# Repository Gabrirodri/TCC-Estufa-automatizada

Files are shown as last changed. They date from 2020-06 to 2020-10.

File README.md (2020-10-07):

# TCC-Estufa-automatizada 2016
## Projeto de TCC de eletroeletronica, automação de estufa 

Um sistema de irrigação controlado por um PIC 18F4550.
Sistema que faz a leitura de valores gravados na EPROM(memória), 
que podem ser alterados pelo usuário através de um painel, e faz um controle de temperatura e da irrigação, 
levando em conta se o solo está com a quantidade de água adequada.

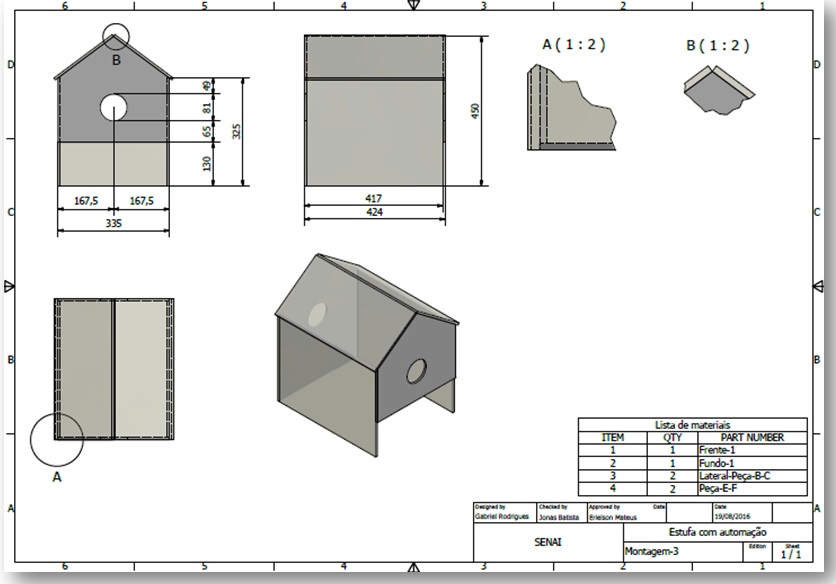
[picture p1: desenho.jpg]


## Checklist
- [X] Planejamento (Ideias de projeto, plano de ação, 5W2H)
- [X] Orçamento
- [X] Montagem do Cronograma (Divisão das tarefas)
- [X] Fluxograma
- [X] Pesquisa
- [X] Desenho da estrutura
- [X] Desenho do Circuito
- [X] Com base no fluxograma, pensar na logica de programação
- [X] Ler o Datasheet do PIC e consultar sempre quando necessario
- [X] Montagem da logica do menu
- [X] Montagem do keypad com LCD
- [X] Programação dos sensores
- [X] Aquisições de materiais, componentes, acrilicos
- [X] Fazer cortes necessarios dos acrilicos
- [X] Fazer cortes das calhas
- [X] Montagem fisica do projeto
- [X] Testes em protoboard
- [X] Confecção das placas de circuito
- [X] Soldagem de componentes
- [X] Interligação eletrica
- [X] Testes no caimento da agua das calhas
- [X] Testes no circuito: sensores, Keypad, LCD, Reles, Bomba d'agua
- [X] Correções no projeto
- [X] Testes em geral
- [X] Confecção dos manuais

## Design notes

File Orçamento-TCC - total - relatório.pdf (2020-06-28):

Materiais | Quantidade | Preço Unidade | Preço Final
Cooler | 2 | R$ 10,00 | R$ 20,00
PIC 18F4550 | 1 | R$ 40,15 | R$ 40,15
Display LCD 16x4 | 1 | R$ 16,00 | R$ 16,00
Teclado Matricial (Keypad) | 1 | R$ 13,00 | R$ 13,00
Botão de Emergência | 1 | R$ 15,00 | R$ 15,00
Bomba para Gotejamento | 1 | R$ 21,00 | R$ 21,00
Bomba para Nebulização | 1 | R$ 45,00 | R$ 45,00
Reservatório | 1 | R$ 25,00 | R$ 25,00
Acrílico | 4 | R$ 40,00 | R$ 160,00
Mangueiras | 1,5 metros | R$ 0,60 | R$ 0,90
Resistência Elétrica | 1 | R$ 30,00 | R$ 30,00
Caixa Plástica | 1 | R$ 20,00 | R$ 20,00
Caixa | 1 | R$ 30,00 | R$ 30,00
Base de Madeira | 1 | R$ 65,00 | R$ 65,00
Cano de PVC | 1,5 metros | R$ 10,00 | R$ 15,00
LED | 6 | R$ 1,50 | R$ 9,00
Sensor de Temperatura e Umidade | 1 | R$ 6,00 | R$ 6,00
Push button | 6 | R$ 3,00 | R$ 18,00
Sensor de Umidade | 1 | R$ 10,00 | R$ 10,00
Total | | | R$ 559,05

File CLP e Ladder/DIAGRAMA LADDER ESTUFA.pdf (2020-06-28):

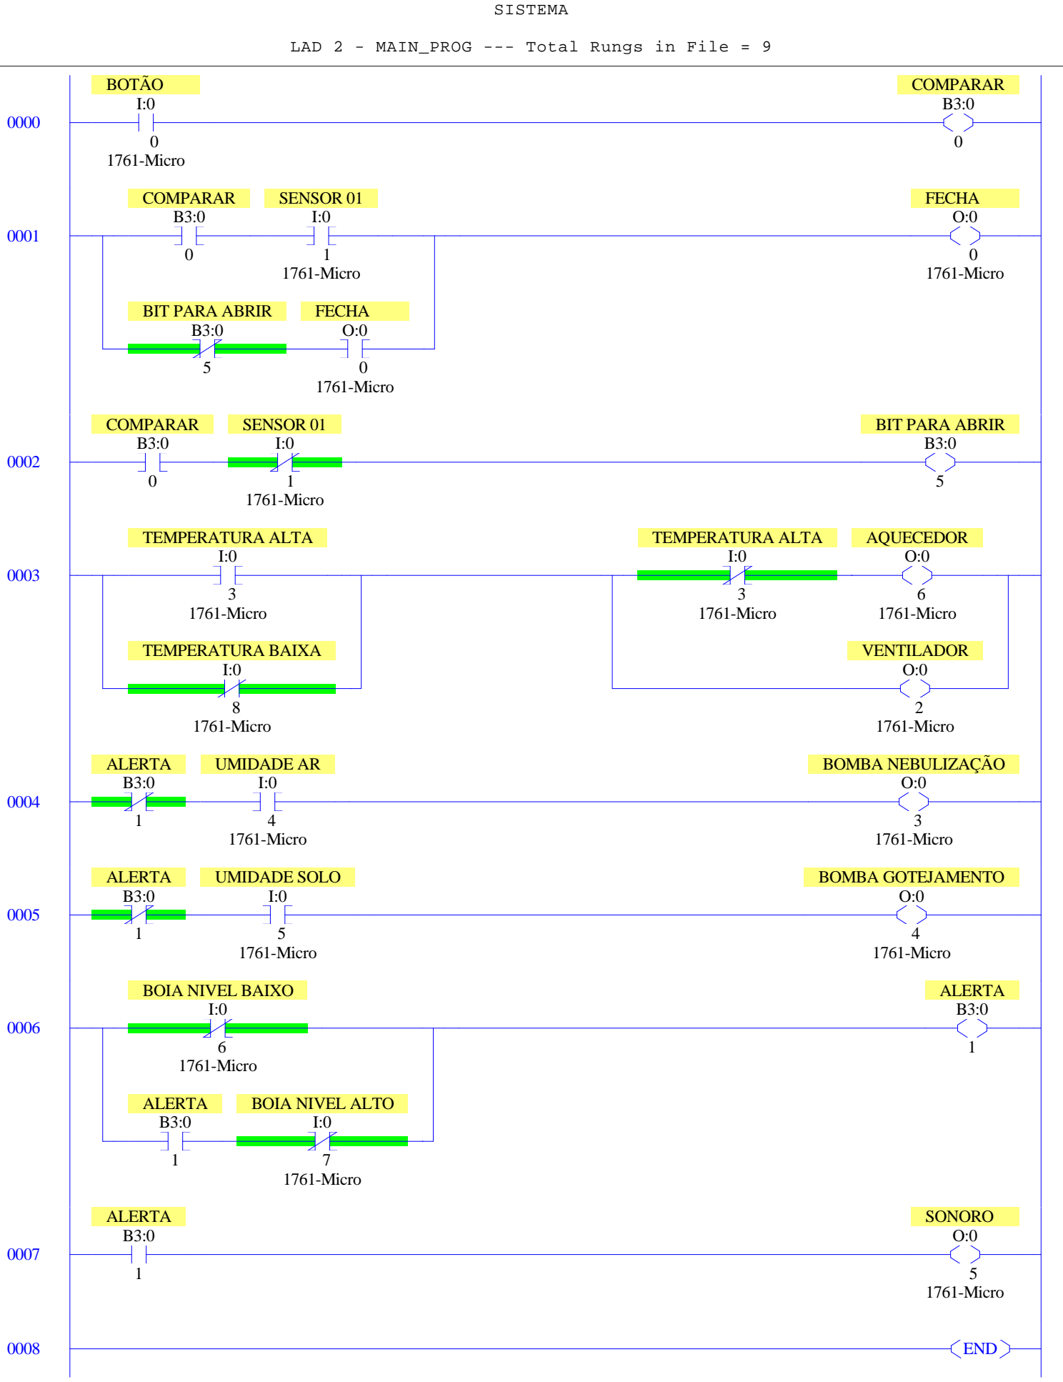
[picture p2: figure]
SISTEMA; 0 1761-Micro; BOTÃO; COMPARAR; 1 1761-Micro; SENSOR 01; BIT PARA ABRIR; FECHA; 3 1761-Micro; TEMPERATURA ALTA; 8 1761-Micro; TEMPERATURA BAIXA; 6 1761-Micro; AQUECEDOR; 2 1761-Micro; VENTILADOR; ALERTA; 4 1761-Micro; UMIDADE AR; BOMBA NEBULIZAÇÃO; 5 1761-Micro; UMIDADE SOLO; BOMBA GOTEJAMENTO; BOIA NIVEL BAIXO; 7 1761-Micro; BOIA NIVEL ALTO; SONORO; END

LAD 2 - MAIN_PROG --- Total Rungs in File = 9

Page 0 | Monday, October 31, 2016 - 15:10:52

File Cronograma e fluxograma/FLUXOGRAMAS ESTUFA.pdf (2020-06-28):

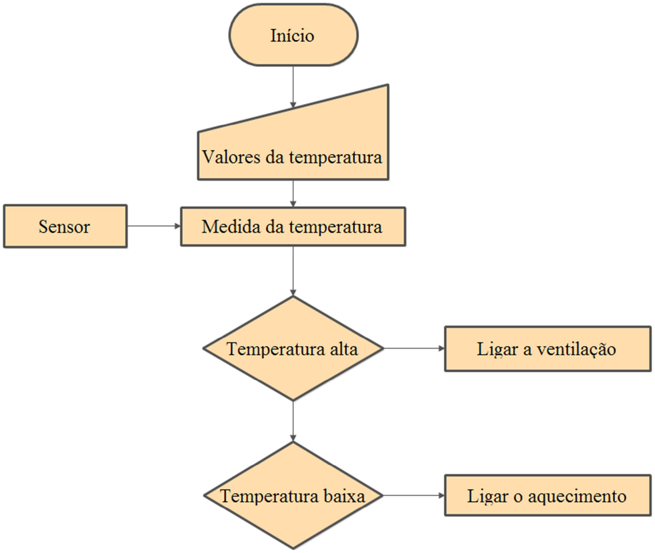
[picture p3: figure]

Lógica do controle de temperatura

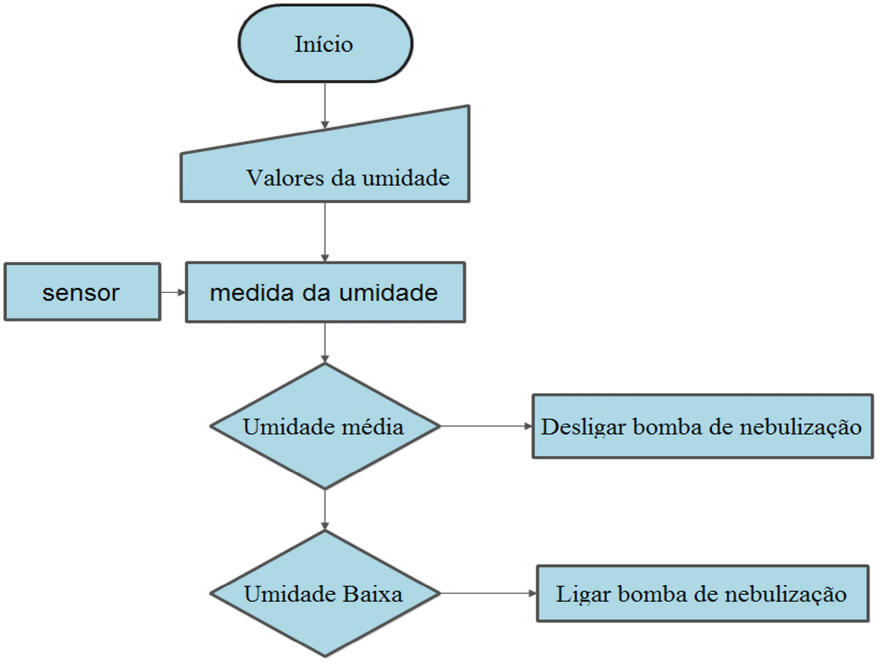
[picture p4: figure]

Lógica do controle de umidade

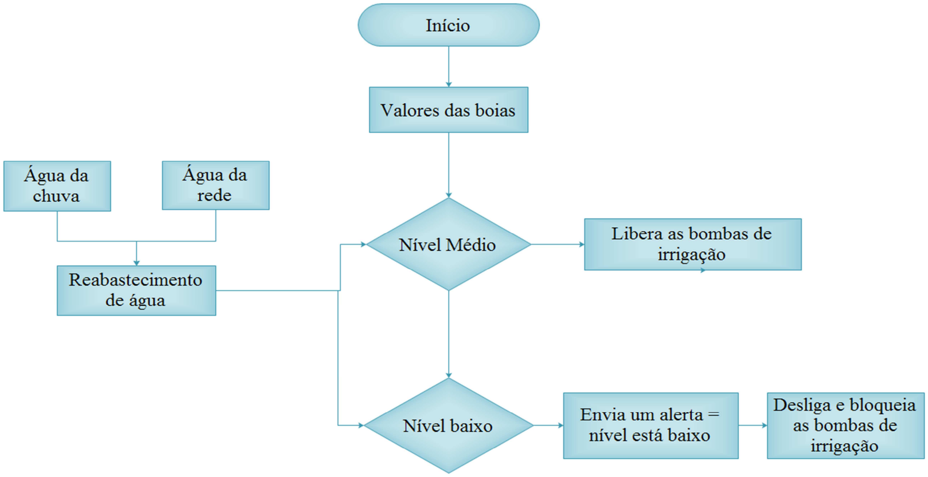
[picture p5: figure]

Lógica do controle de nível

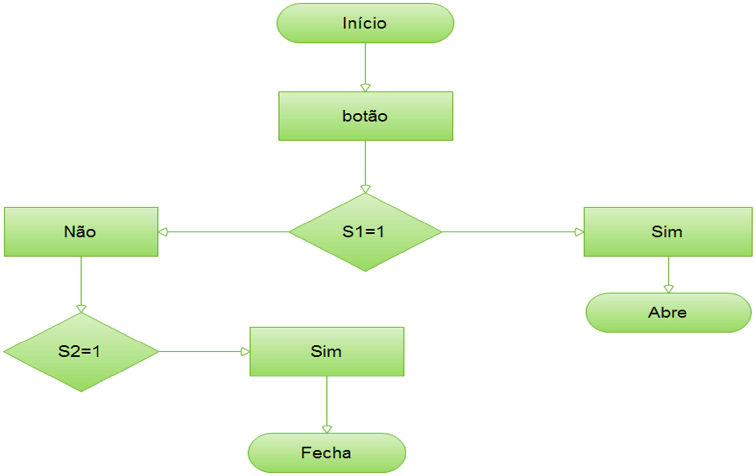
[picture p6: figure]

Lógica do controle da porta

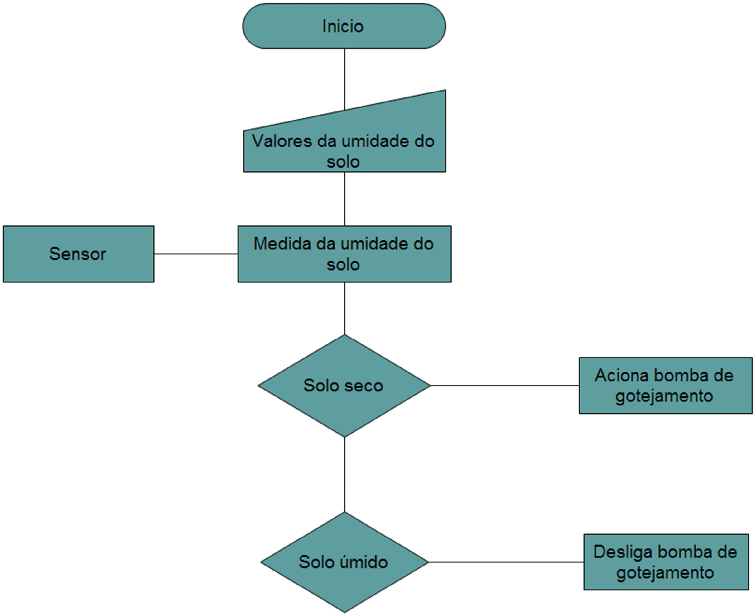
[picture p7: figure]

Controle de umidade do solo

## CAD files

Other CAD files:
TCC/Assembly1.iam
TCC/Assembly2.iam
TCC/Frente inferior - porta.ipt
TCC/Frente inferior - porta1.ipt
TCC/Frente-inferior-E-D.ipt
TCC/Montagem-2.idw
TCC/Montagem-3.idw
TCC/Montagem.iam
TCC/Montagem.idw
TCC/OldVersions/Montagem-3.0001.idw
TCC/OldVersions/Montagem.0001.idw
TCC/OldVersions/Montagem.0004.iam
TCC/OldVersions/Peças frente inferior.0001.idw
TCC/OldVersions/frente.0003.ipt
TCC/OldVersions/fundo-1.0001.idw
TCC/OldVersions/fundo.0003.ipt
TCC/OldVersions/teto01.0006.ipt
TCC/Peças frente inferior.idw
TCC/frente-1.idw
TCC/frente.idw
TCC/frente.ipt
TCC/fundo-1.idw
TCC/fundo.idw
TCC/fundo.ipt
TCC/lateral-peça-b-c.idw
TCC/lateral.ipt
TCC/teto01.idw
TCC/teto01.ipt
TCC/teto02.ipt

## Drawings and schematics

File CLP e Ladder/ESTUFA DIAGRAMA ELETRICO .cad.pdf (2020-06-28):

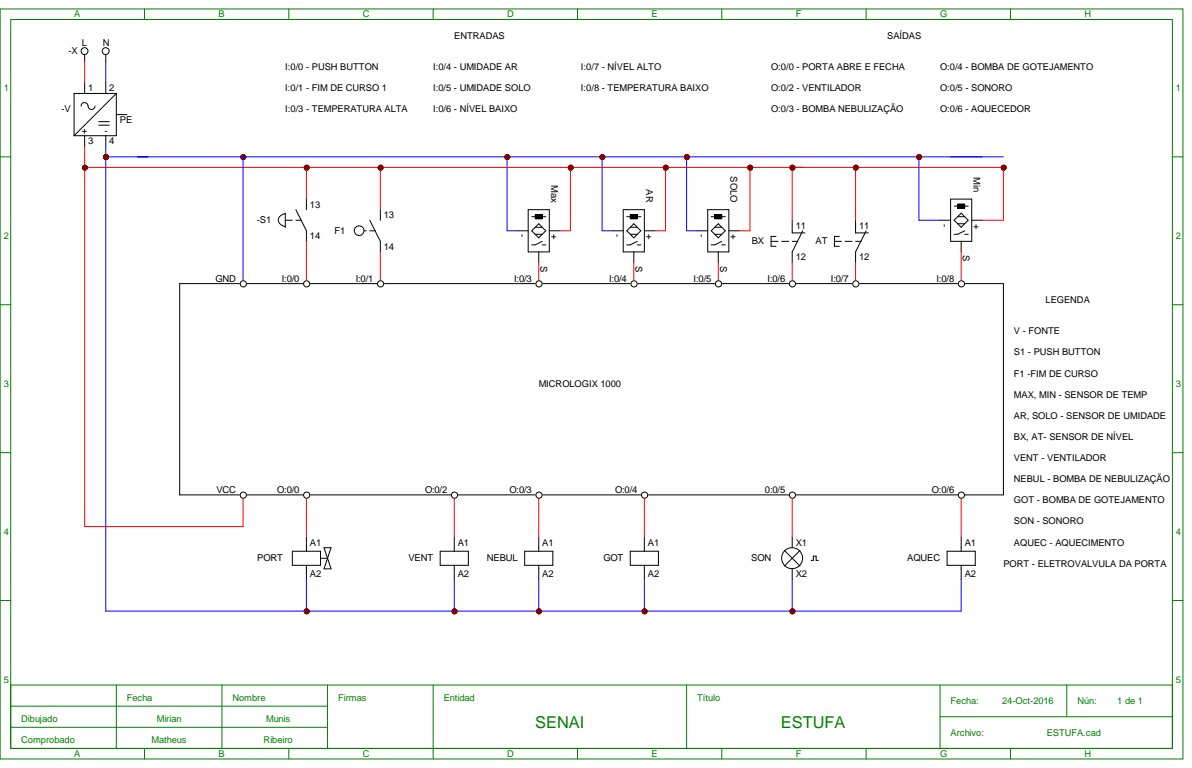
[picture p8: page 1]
Archivo:; ESTUFA.cad; SON; VENT; NEBUL; GOT; AQUEC; Max +-; Min +-; SOLO +-; MICROLOGIX 1000; V - FONTE; S1 - PUSH BUTTON; VENT - VENTILADOR; SON - SONORO; AQUEC - AQUECIMENTO; LEGENDA; I:0/0 - PUSH BUTTON; I:0/3 - TEMPERATURA ALTA; I:0/4 - UMIDADE AR; I:0/5 - UMIDADE SOLO; I:0/6 - NÍVEL BAIXO; I:0/7 - NÍVEL ALTO; I:0/8 - TEMPERATURA BAIXO; O:0/2 - VENTILADOR; O:0/3 - BOMBA NEBULIZAÇÃO; O:0/6 - AQUECEDOR; O:0/5 - SONORO; PORT; GND; VCC

L -X | | ENTRADAS SAÍDAS N

O:0/0 - PORTA ABRE E FECHA

O:0/4 - BOMBA DE GOTEJAMENTO

I:0/1 - FIM DE CURSO 1

F1 -FIM DE CURSO

MAX, MIN - SENSOR DE TEMP

AR, SOLO - SENSOR DE UMIDADE

BX, AT- SENSOR DE NÍVEL

NEBUL - BOMBA DE NEBULIZAÇÃO

GOT - BOMBA DE GOTEJAMENTO

PORT - ELETROVALVULA DA PORTA

Fecha | Nombre | Firmas | Entidad SENAI | Título ESTUFA | Fecha: 24-Oct-2016 | Nún: 1 de 1

Dibujado | Mirian | Munis

Comprobado | Matheus | Ribeiro

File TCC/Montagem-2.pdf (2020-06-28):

B ( 1 : 1 )

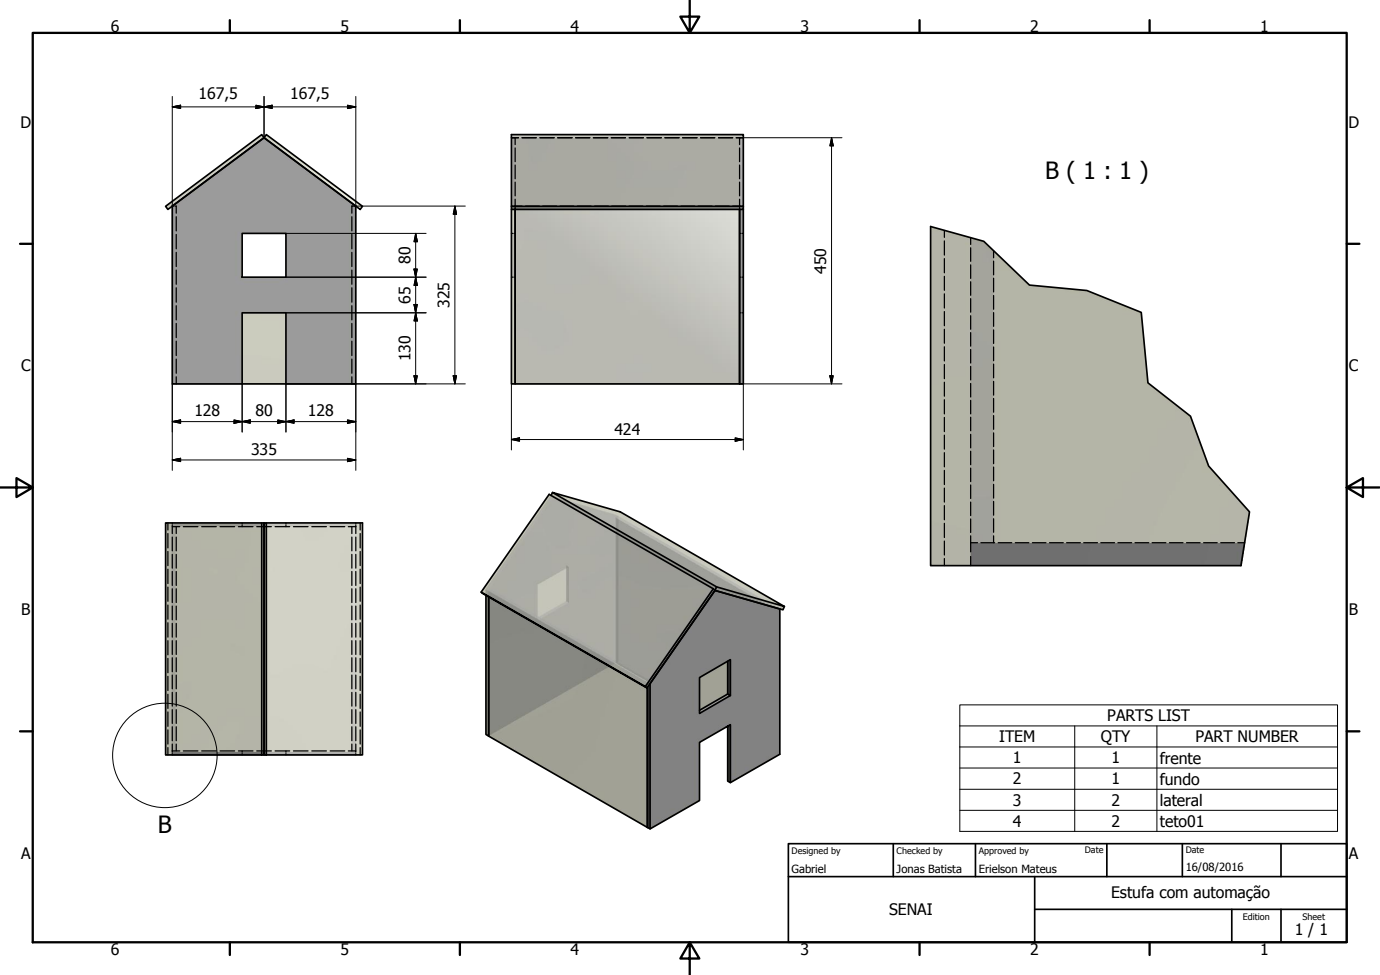
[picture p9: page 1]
PARTS LIST; ITEM; QTY; PART NUMBER; frente; fundo; lateral; teto01; SENAI; Gabriel; Jonas Batista; Erielson Mateus; Designed by; Checked by; Approved by; Date; Edition; Sheet

Estufa com automaomo

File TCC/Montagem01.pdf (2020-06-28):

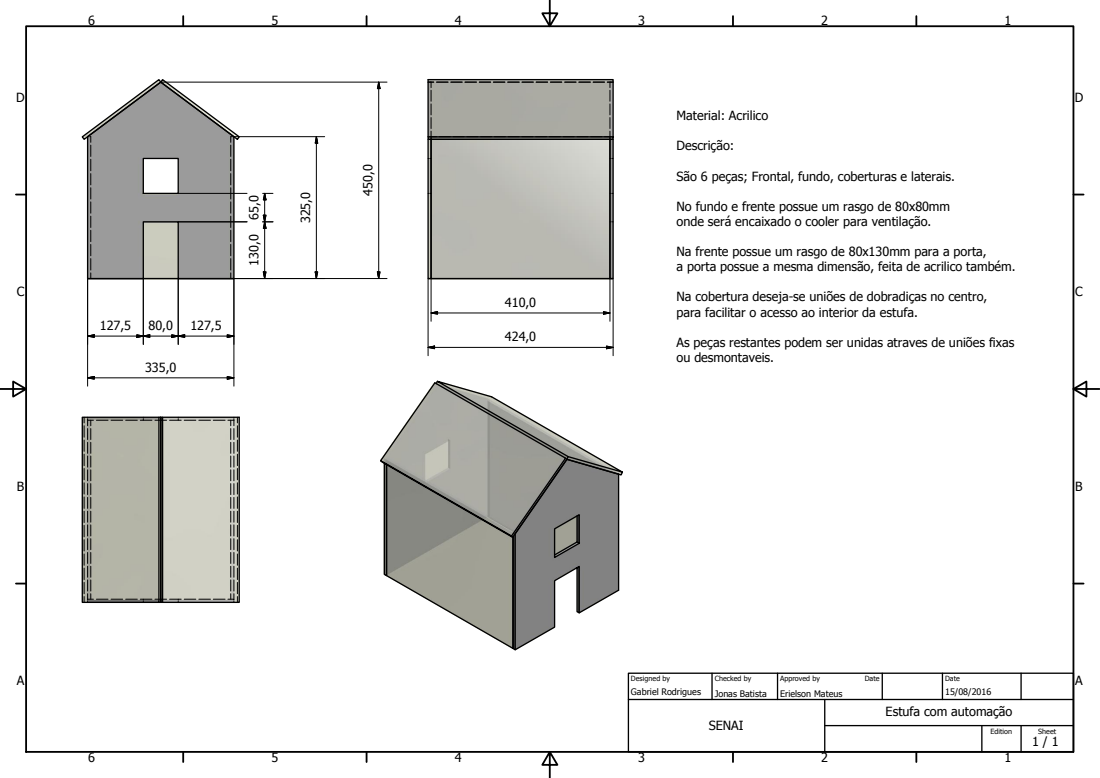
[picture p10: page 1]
SENAI; Gabriel Rodrigues; Jonas Batista; Erielson Mateus; Designed by; Checked by; Approved by; Date; Edition; Sheet; Material: Acrilico; Descriomo:

Smo 6 peoas; Frontal, fundo, coberturas e laterais.

No fundo e frente possue um rasgo de 80x80mm
onde seri encaixado o cooler para ventilaomo.

Na frente possue um rasgo de 80x130mm para a porta,
a porta possue a mesma dimensmo, feita de acrilico tambpm.

Na cobertura deseja-se uni}es de dobradioas no centro,
para facilitar o acesso ao interior da estufa.

As peoas restantes podem ser unidas atraves de uni}es fixas
ou desmontaveis.

Estufa com automaomo

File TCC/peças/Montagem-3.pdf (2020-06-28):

A ( 1 : 2 ) | B ( 1 : 2 )
B

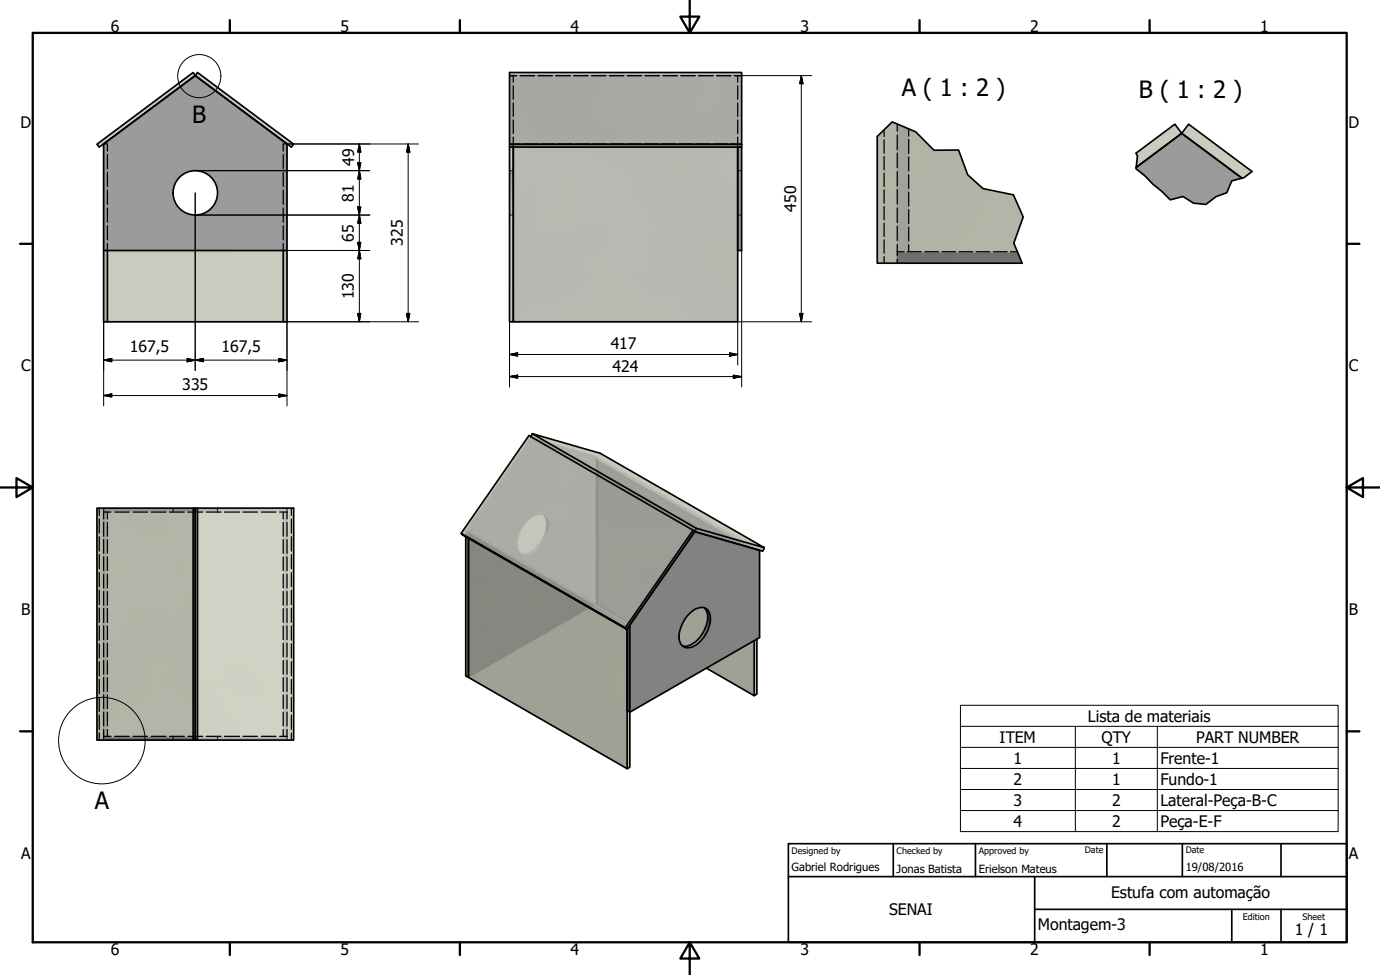
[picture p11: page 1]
ITEM; QTY; PART NUMBER; Frente-1; Fundo-1; Lateral-Peoa-B-C; Peoa-E-F; Montagem-3; SENAI; Gabriel Rodrigues; Jonas Batista; Erielson Mateus; Designed by; Checked by; Approved by; Date; Edition; Sheet

Lista de materiais

Estufa com automaomo

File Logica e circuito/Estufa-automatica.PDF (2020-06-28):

U1

U2

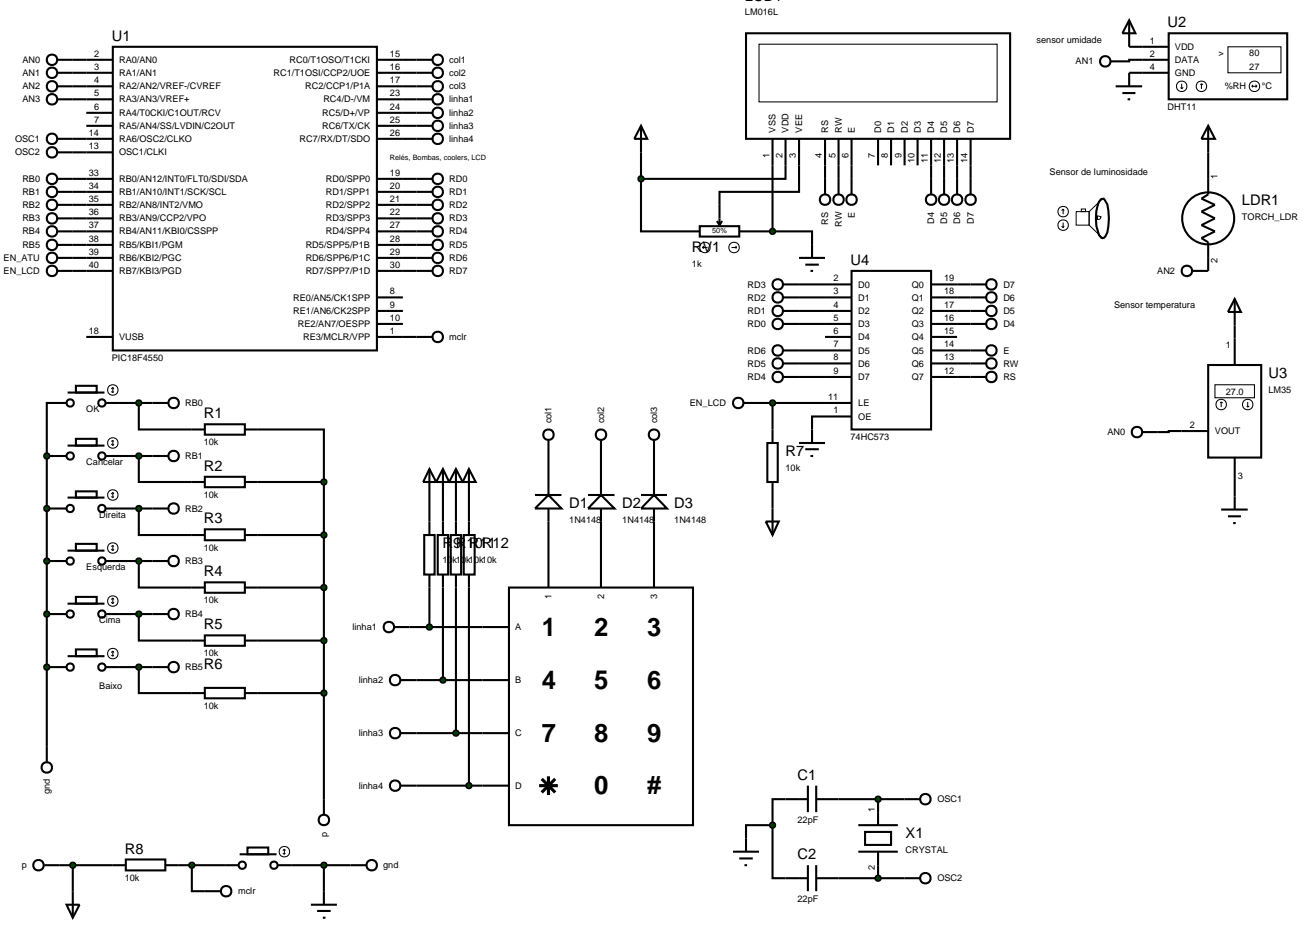
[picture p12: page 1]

Relés, Bombas, coolers, LCD

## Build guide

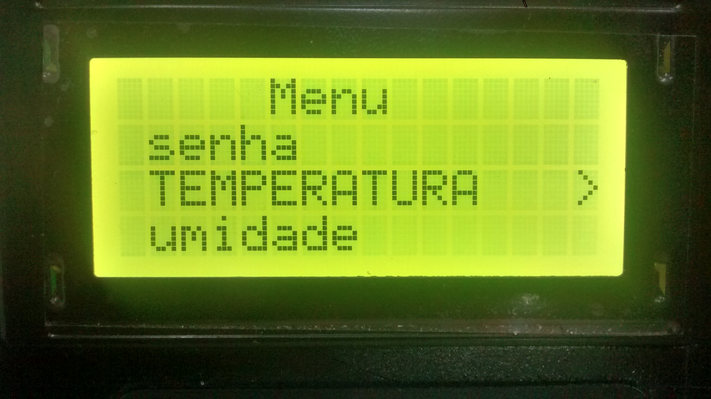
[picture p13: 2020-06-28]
Manual da estufa/IMG_20161124_165332127_HDR.jpg

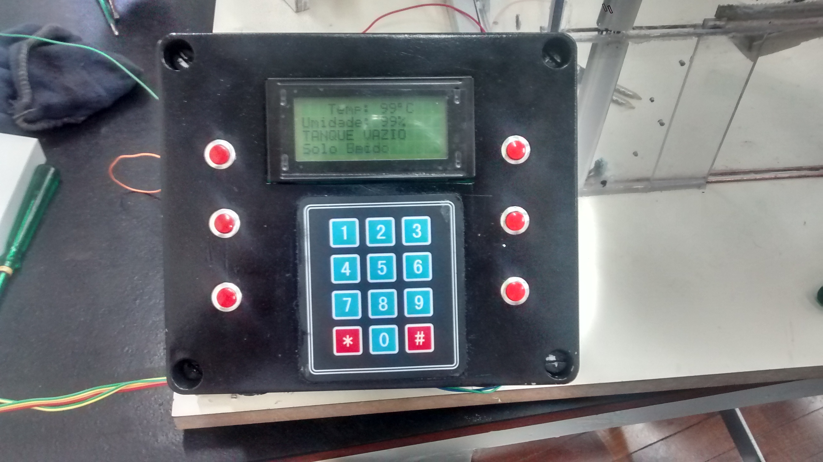
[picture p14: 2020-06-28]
Manual da estufa/IMG_20161124_165251841_HDR.jpg

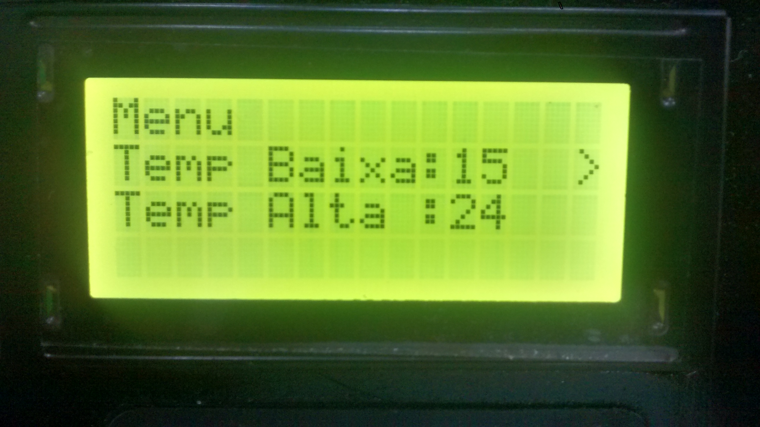
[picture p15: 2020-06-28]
Manual da estufa/IMG_20161124_165404496_HDR.jpg

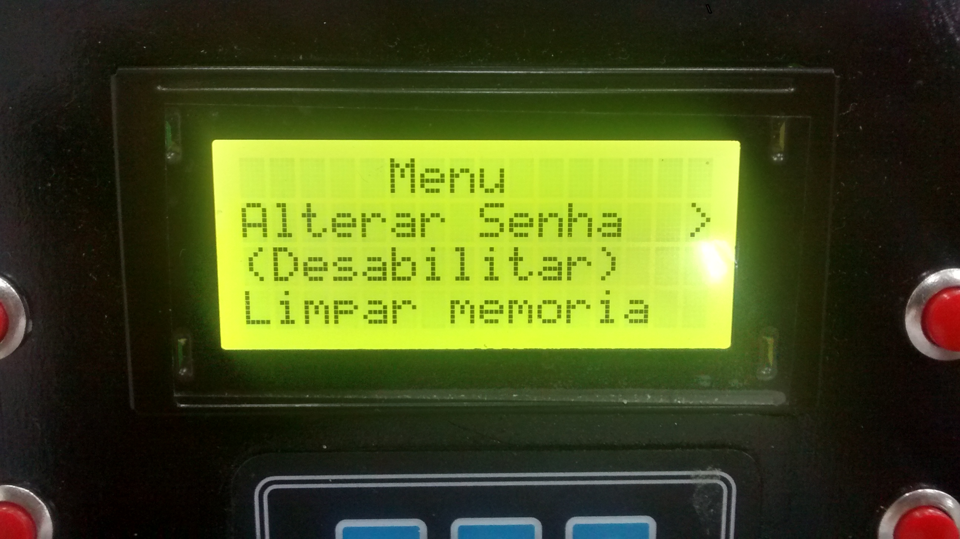
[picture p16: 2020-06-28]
Manual da estufa/IMG_20161124_165452365_HDR.jpg

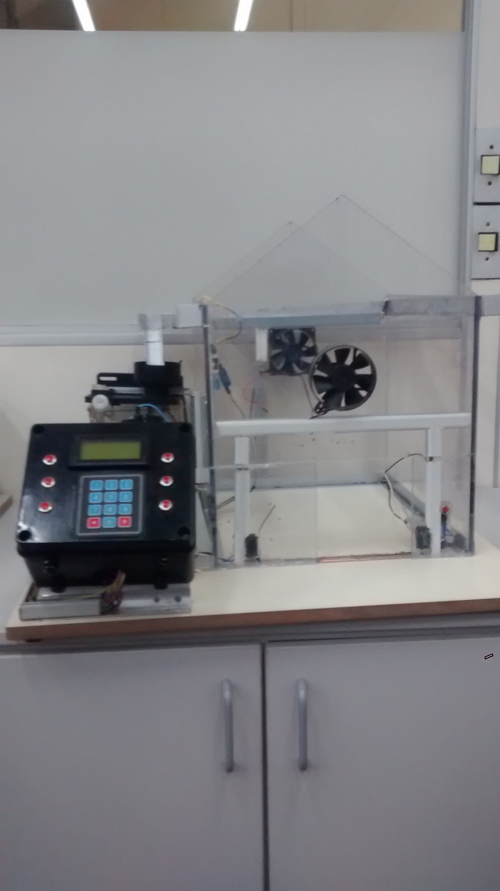
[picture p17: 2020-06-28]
Manual da estufa/IMG_20161129_171212629.jpg

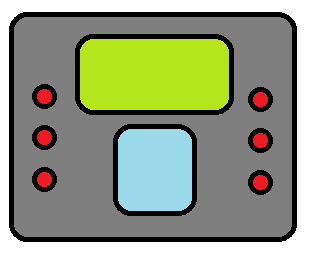
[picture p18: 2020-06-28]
Manual da estufa/painelfoto.png

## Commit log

2020-06-28 Add files via upload
    Desenhos
    [Assembly1.iam, Assembly2.iam, Frente inferior - porta.ipt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]
2020-06-28 Add files via upload
    Manuais para o usuario
2020-06-28 Add files via upload
    Projeto em CLP - Diagrama ladder e eletrico, embora o projeto tenha sido feito em microcontrolador, essa seria a logica de funcionamento em clp... um funcionamento mais basico...
2020-06-28 Add files via upload
    Funcionamento do circuito
